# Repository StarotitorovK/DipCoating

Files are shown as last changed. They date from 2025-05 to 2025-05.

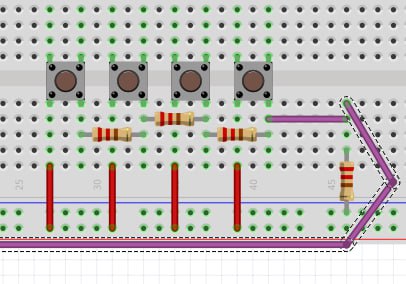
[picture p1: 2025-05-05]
Documentation/keyboard.jpg

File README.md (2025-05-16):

# DipCoater
------
Проект по практикуму цифрового производства

Прибор для нанесения тонких пленок методом dip-coating

Авторы:
	Старотиторов К.С., Б04-301
	Огай В.А., Б04-303

TG-канал: t.me/dip_coating

## Описание проекта

Поставленные задачи: 
выбрать доступный на рынке электромотор и систему преобразования вращательного движения в поступательное; определиться с основными материалами для производства, спроектировать основные узлы установки; изготовить детали и собрать установку; провести испытания в режиме proof of concept.

Описание установки:
продукт представляет собой устройство, состоящее из:

-	Корпуса, выполняющего также роль подставки для сосуда с мембранной массой;
-	Экрана с клавиатурой, с помощью которых настраиваются скорости погружения и вытягивания образца, а также время нахождения его в жидкости;
-	Рейки с мотором, к которой должен крепиться образец.






Используемый инструментарий:
3D-принтер, паяльная станция, профилометр 

Проблемы, с которыми мы встретились:
- Использование нескольких потребителей энергии добавляет сложностей в проектировке питания и запитки потребителей от одного источника.
- Для точности перемещения рейки требуется хорошая подгонка рейки в рельсе к шестерне.
- При переносе схемы клавиатуры с макетной платы вероятно изменились рассчитанные нами сопротивления, так что клавиатура сбоит и немного шумит, однако функционал может продемонстрировать.

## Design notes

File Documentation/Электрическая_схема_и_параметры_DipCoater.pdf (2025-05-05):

# Электрическая схема и параметры DipCoater

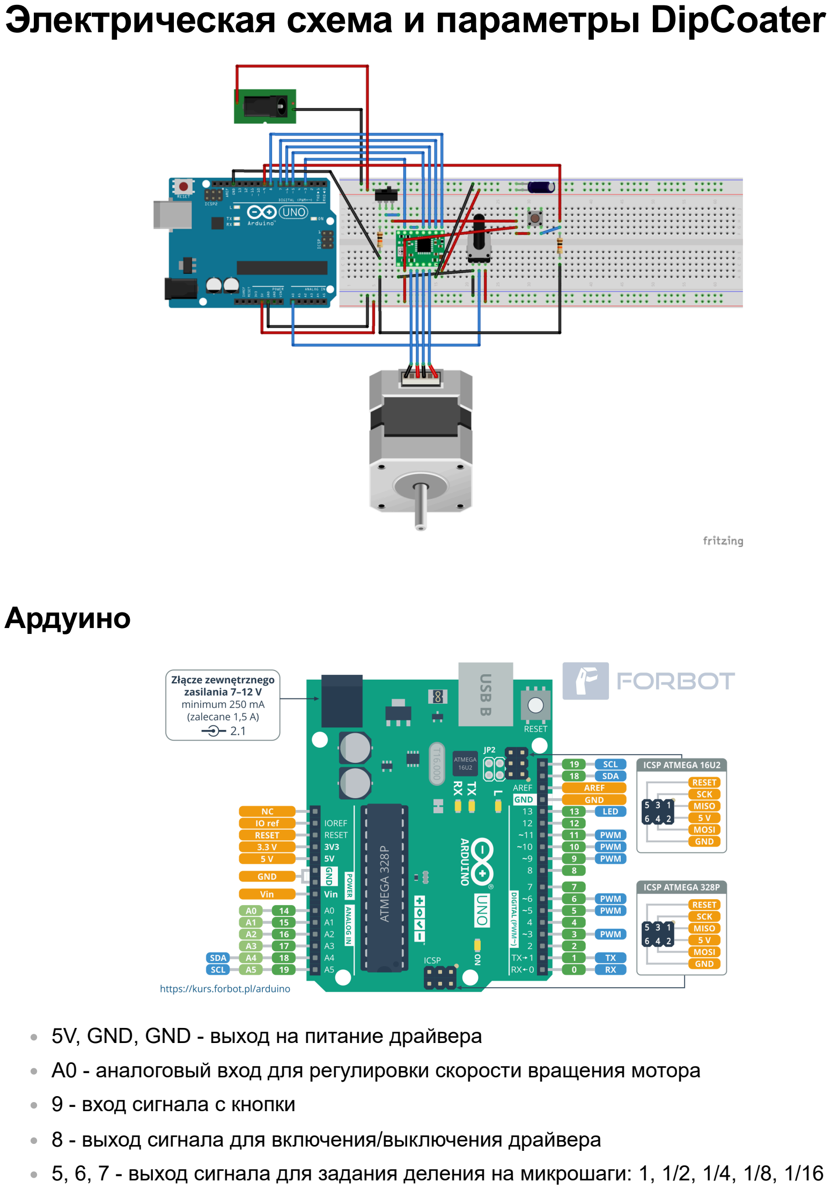
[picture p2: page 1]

## Ардуино

5V, GND, GND - выход на питание драйвера
A0 - аналоговый вход для регулировки скорости вращения мотора
9 - вход сигнала с кнопки
8 - выход сигнала для включения/выключения драйвера
5, 6, 7 - выход сигнала для задания деления на микрошаги: 1, 1/2, 1/4, 1/8, 1/16

## Драйвер

3 - выход сигнала для поворота вала двигателя

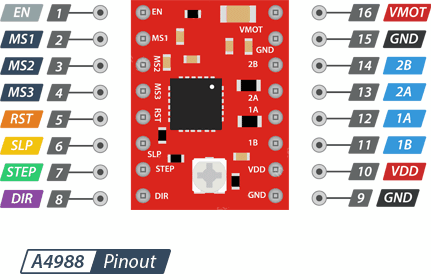
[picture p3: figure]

DIR вход подключен к переключателю: 1 - вращение по часовой стрелке, 0 - против RST и SLP - соединены, т.к. спящий режим не будет использоваться
VDD и GND - питание драйвера; подключены к 5V, GND платы Ардуино соответственно
VMT и GND - питание мотора; подключены через конденсатор 47мкФ к разъему PowerJack
MS1, MS2, MS3 - режим микрошага
1A, 1B, 2A, 2B - питание на обмотки электродвигателя
EN - включение/выключение драйвера: 0 - вкл, 1 - выкл STEP - совершение оборота электродвигателя: 1 - оборот.

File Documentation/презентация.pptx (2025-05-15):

## Проект по практикуму цифрового производства: Прибор для нанесения тонких пленок методом dip-coating.

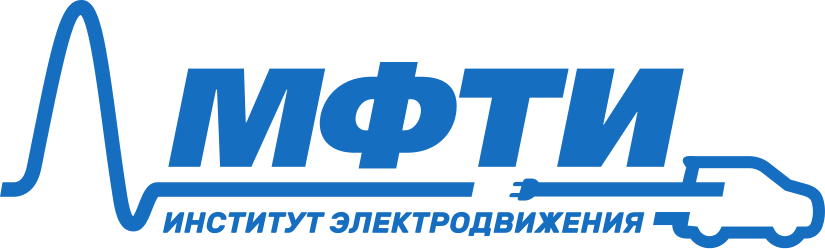
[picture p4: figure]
Изображение выглядит как Шрифт, текст, логотип, Графика Контент, сгенерированный ИИ, может содержать ошибки.

Старотиторов К.С., Огай В.А.
Московский физико-технический институт (НИУ)
2025 г.

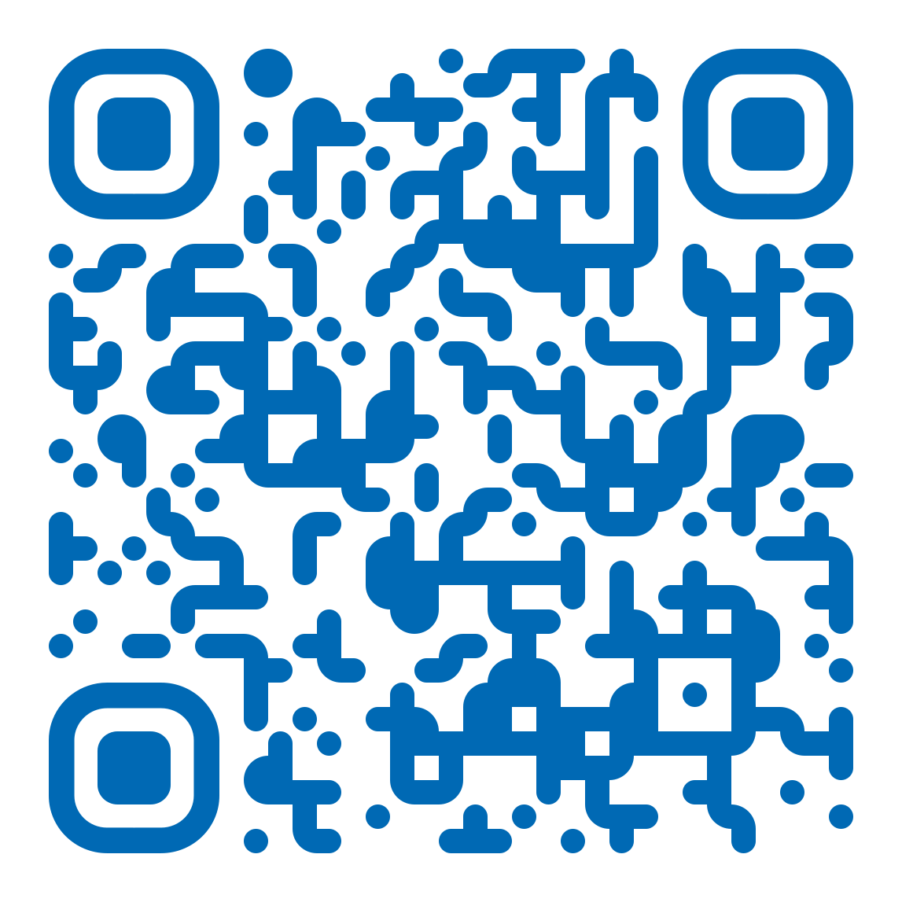
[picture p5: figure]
Изображение выглядит как Графика, Шрифт, типография, Цвет электрик Контент, сгенерированный ИИ, может содержать ошибки.

## Введение

- Литий-ионные аккумуляторы работают за счет перемещения ионов лития между электродами через электролит во время зарядки и разрядки.

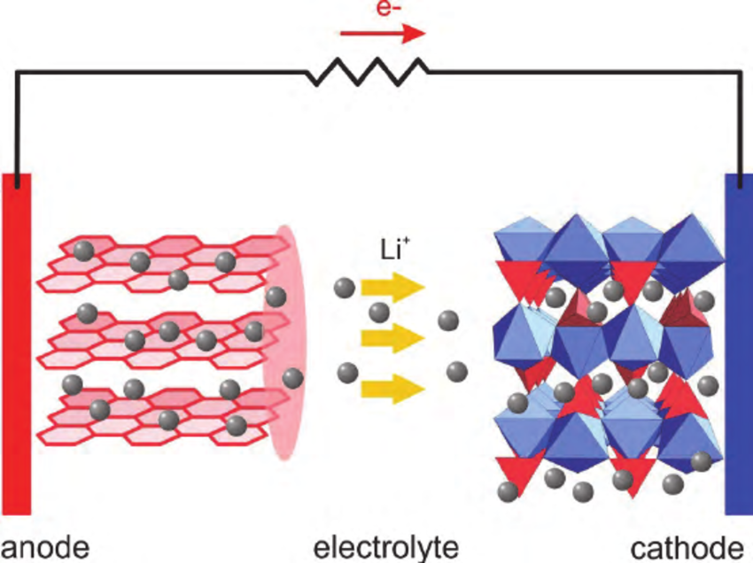
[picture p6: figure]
Working mechanism of Li-ion batteries. The effectiveness of the... | Download Scientific Diagram

## Введение

- Твердотельные литиевые аккумуляторы (ТЛА) – потенциально более безопасная, механически устойчивая и энергоемкая альтернатива классическим литий-ионным аккумуляторам с жидким электролитом (ЛИА)

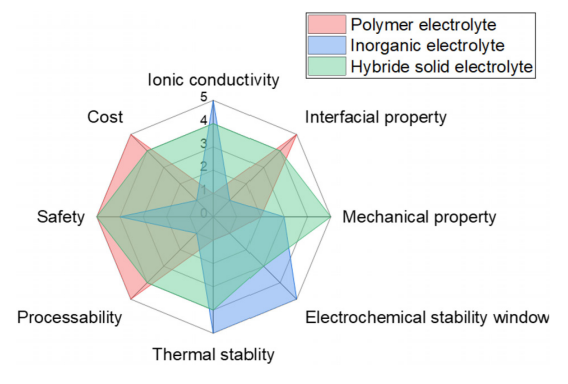
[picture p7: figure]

Неорганические электролиты

Полимерные электролиты

Ионная проводимость

Гибридные электролиты

Стоимость

Межфазное взаимодействие

Безопасность

Механические свойства

Технологичность

Термическая стабильность

Электрохимическая стабильность

## Способы создания мембран

Отдельно стоящая мембрана

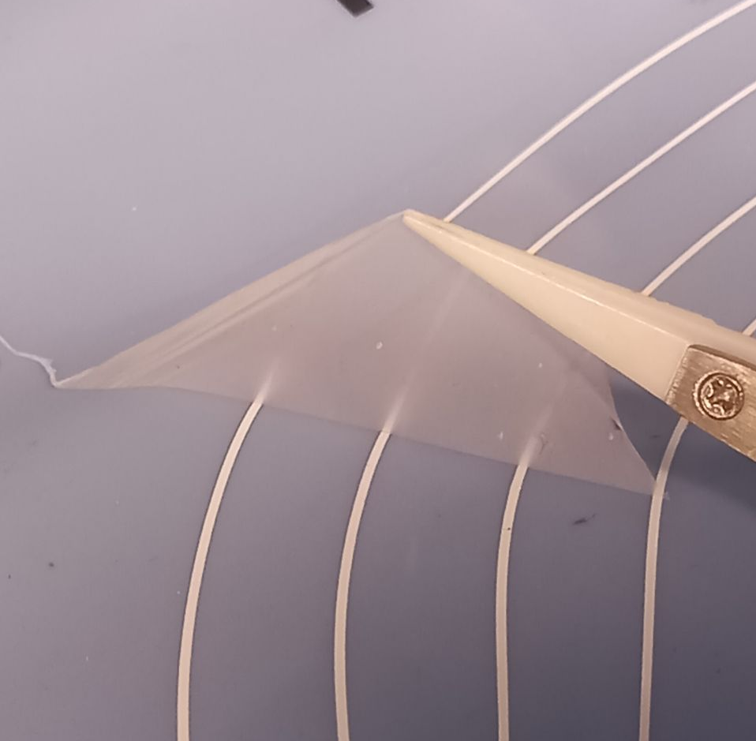
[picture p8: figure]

Spin-coating (на электрод)

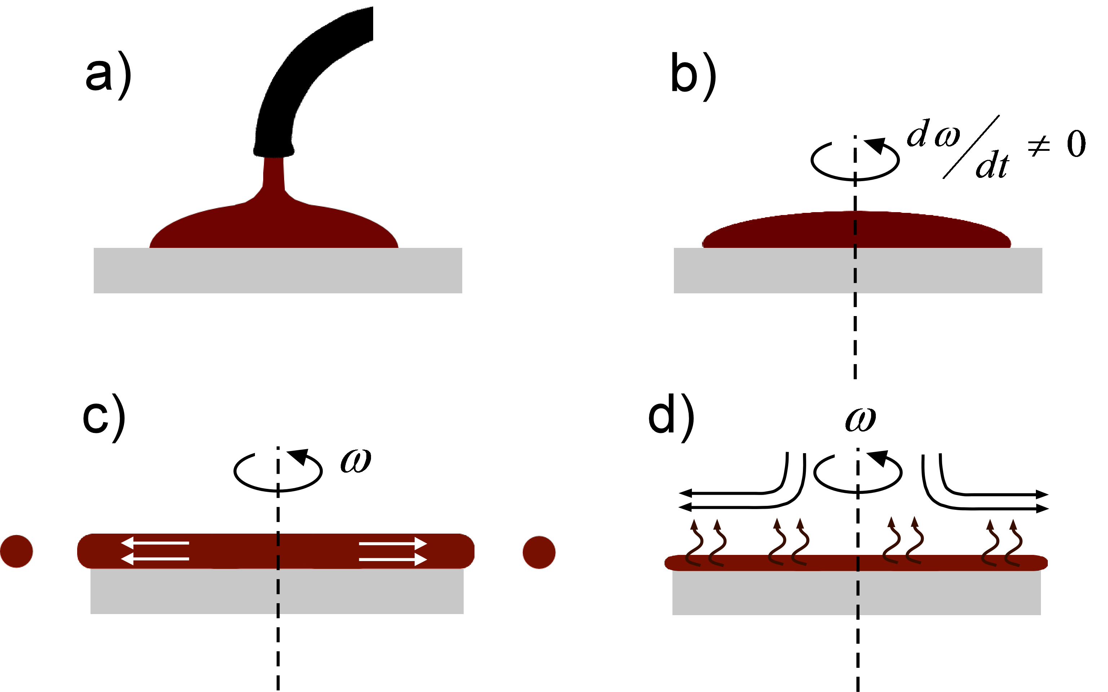
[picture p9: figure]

Blade-coating (на электрод)

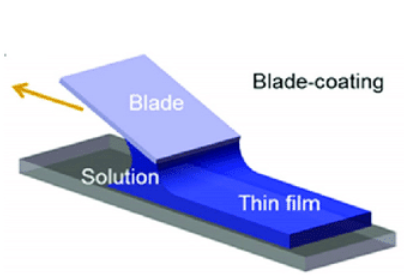
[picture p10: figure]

Dip-coating (на электрод)

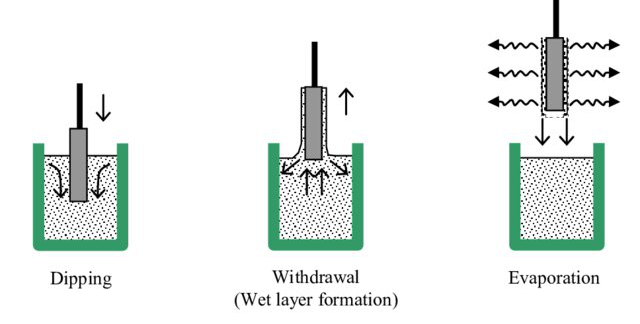
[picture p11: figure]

## Цель проекта и актуальность

- Цель проекта: спроектировать и изготовить прибор для нанесения тонких пленок (мембран) методом dip-coating с диапазоном скоростей покрытия 0,1-10 мм/с для лаборатории пост-литий-ионных электрохимических систем Института Электродвижения МФТИ.
- Актуальность: по предварительным подсчетам, себестоимость итогового продукта не будет превышать 15.000 руб., что в разы дешевле существующих на рынке решений.

## Теоретическая часть

- Зависимость толщины пленки от скорости извлечения, оставшейся на поверхности описывается капиллярной моделью (в области до 0,1 мм/с) и моделью Ландау-Левича (в области более 0,5 мм/с).
- Минимум толщины достигается в переходной области между двумя моделями.

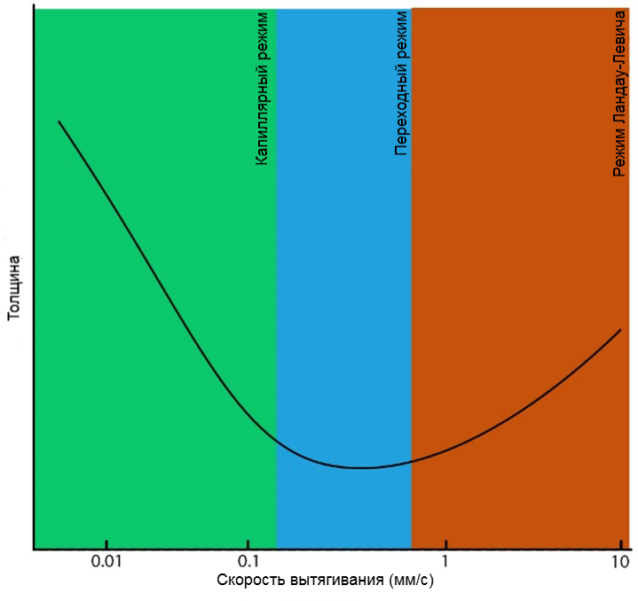
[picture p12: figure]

h=kE/(uL)

h=0,93((uη)^(2/3))/(σ^(1/6) √(ρg))

## Этапы проектирования

1. Разработка концепции работы устройства;
2. Создание прототипа без корпуса на базе Arduino Uno и макетной платы (код);
3. Тестирование прототипа на работоспособность;
4. 3D-моделирование и печать верхней части корпуса, рейки и шестерни;
5. Разработка клавиатуры;
6. 3D-моделирование и печать нижней части корпуса и крышки;
7. Пайка платы клавиатуры с кнопками;
8. Добавление клавиатуры и экрана к основной плате;
9. Итоговая сборка MVP;
10. Тестирование MVP (проверка работоспособности и удобства использования в лабораторных условиях).

## Принцип работы прибора с инженерной точки зрения

- Шаговый двигатель, установленный в корпус, используется для обеспечения движения с постоянной скоростью погружения и вытягивания образца.
- Вращательное движение мотора переводится в поступательное с помощью шестерни и зубчатой рейки, установленной в корпус на рельсу.

## 3D-модели компонентов прибора

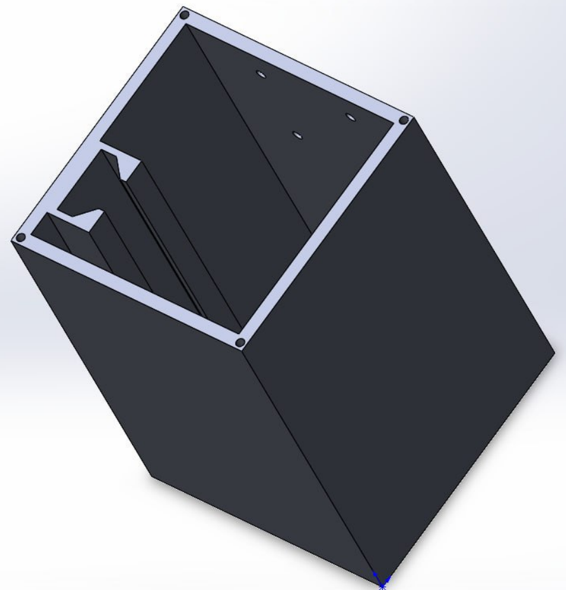
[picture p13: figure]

Корпус с желобом для рельсы и креплением для мотора

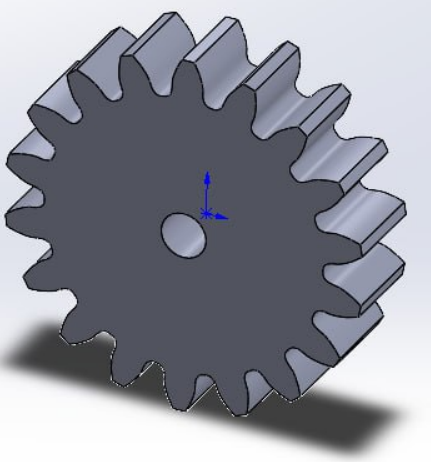
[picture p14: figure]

Шестерня

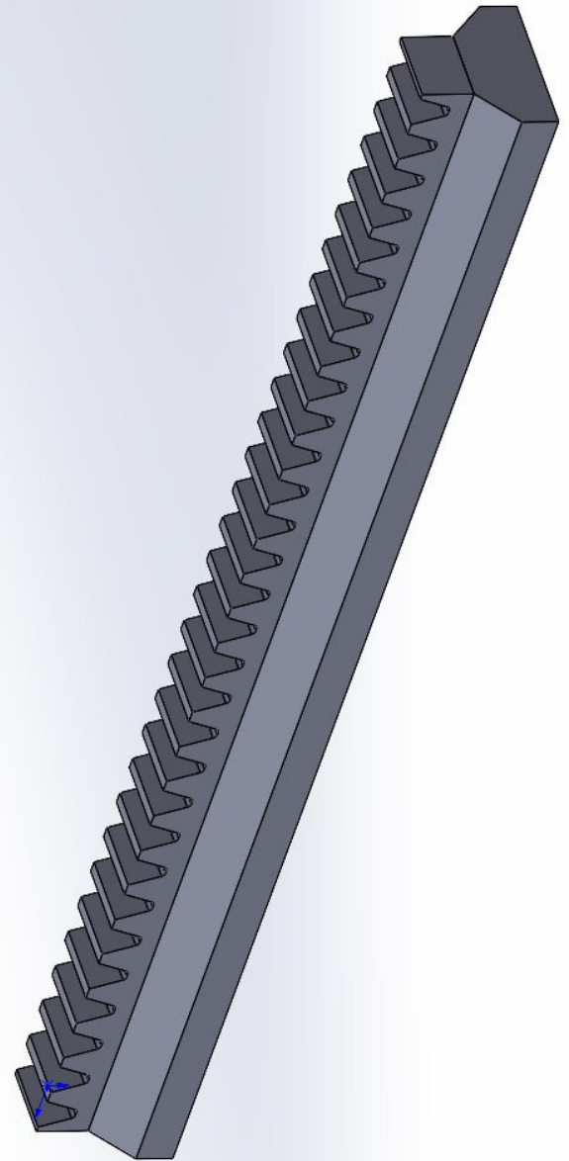
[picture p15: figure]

Зубчатая рейка на рельсе

## 3D-модели компонентов прибора

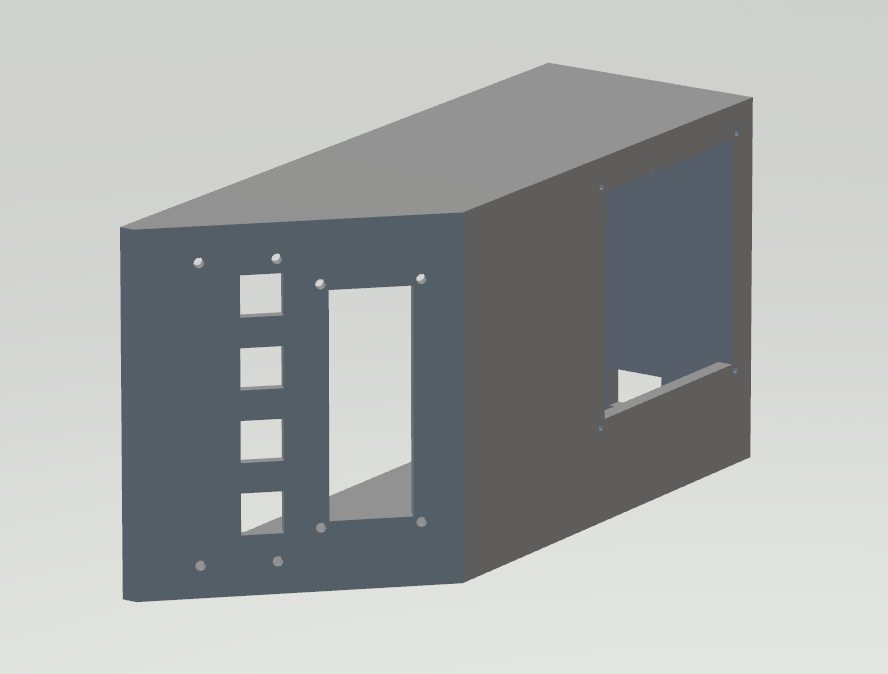
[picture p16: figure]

Нижняя часть корпуса

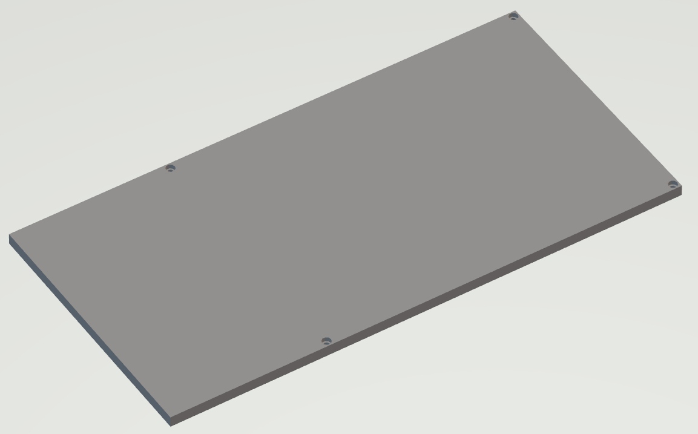
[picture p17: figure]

Крышка

## Аппаратная часть

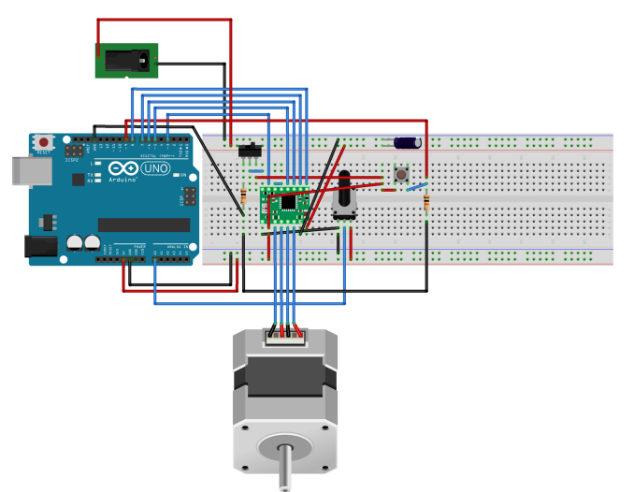
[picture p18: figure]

- Основными компонентами установки являются шаговый двигатель и плата Arduino Uno с драйвером, контролирующая его. Дополнительно возможно заменить используемую макетную плату на печатную, выполненную на заказ.

## Аппаратная часть (экран и клавиатура)

## Результаты тестирования

LiTFSI : PEO = 1 : 7,25

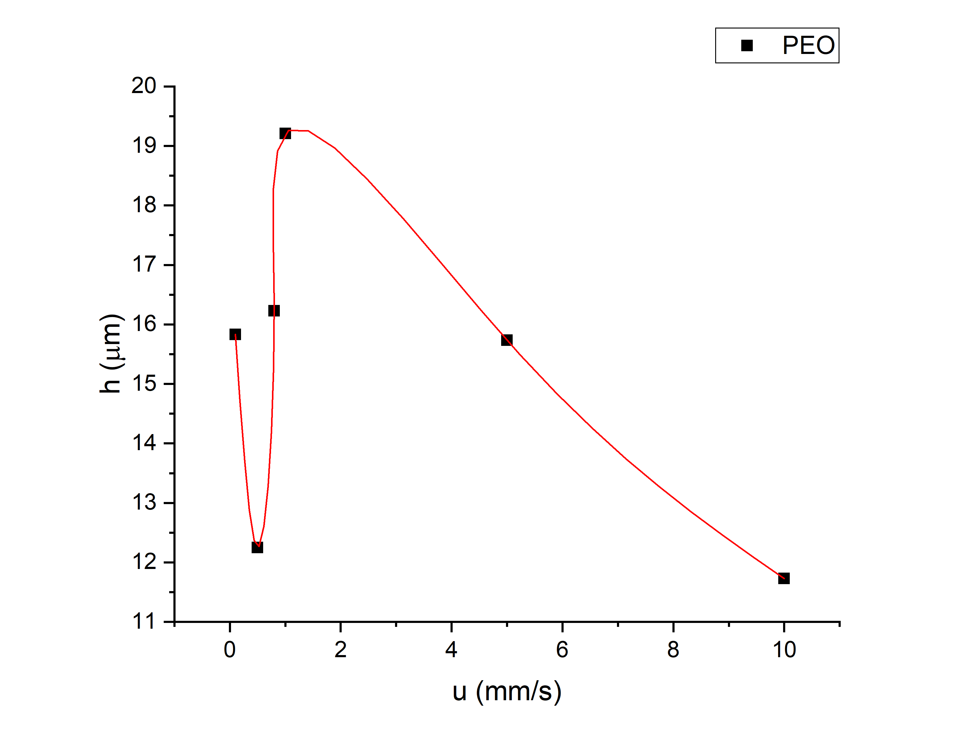
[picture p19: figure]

LiTFSI : SN : EO = 1 : 4 : 16

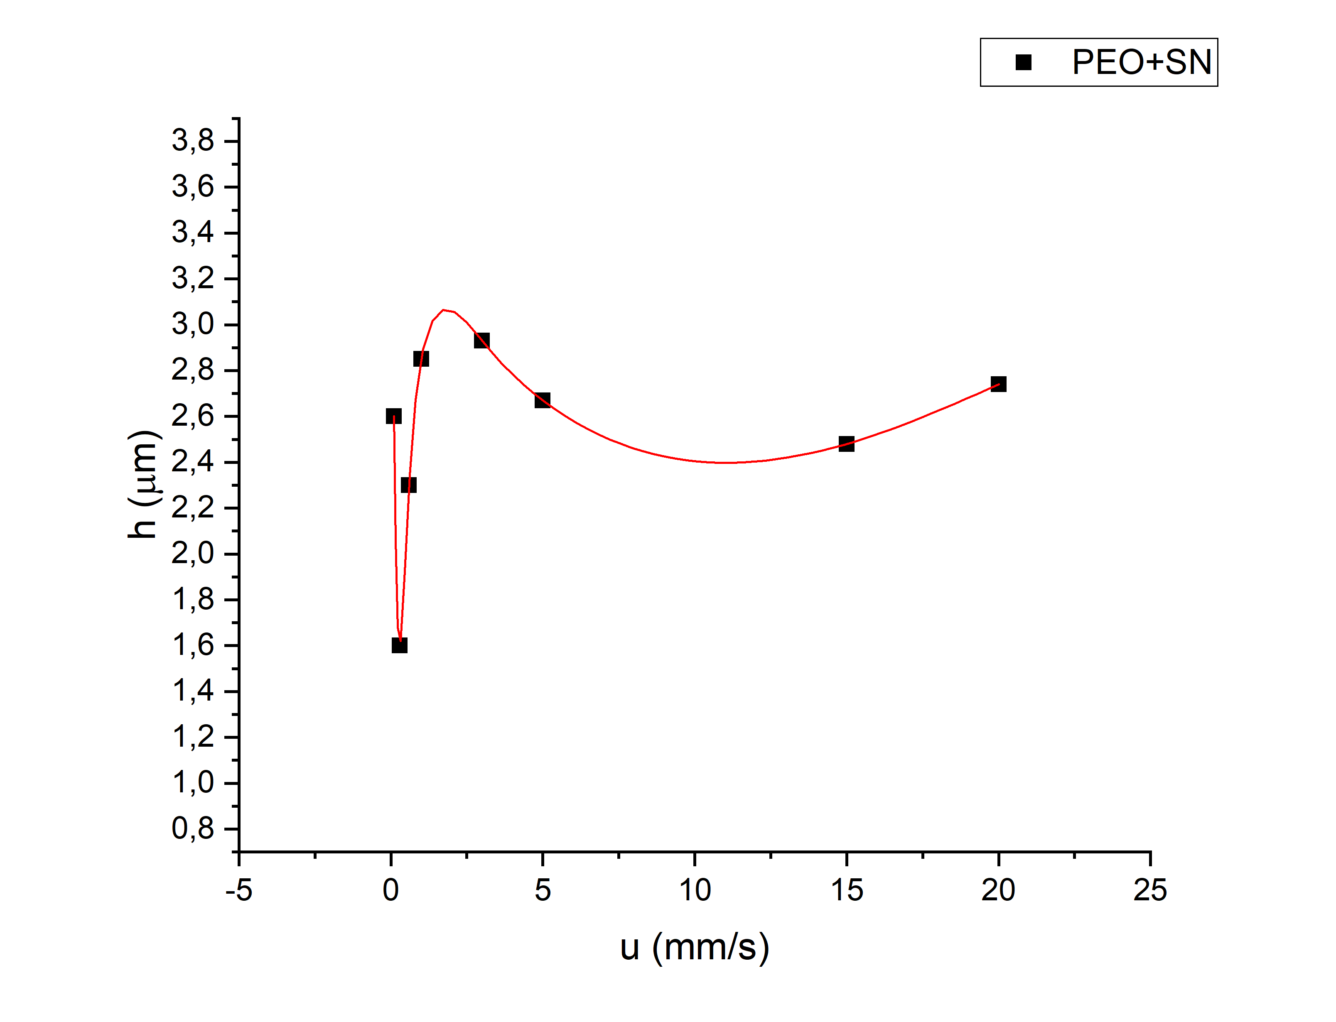
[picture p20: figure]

## Результаты тестирования

LiTFSI : PEO = 1 : 7,25

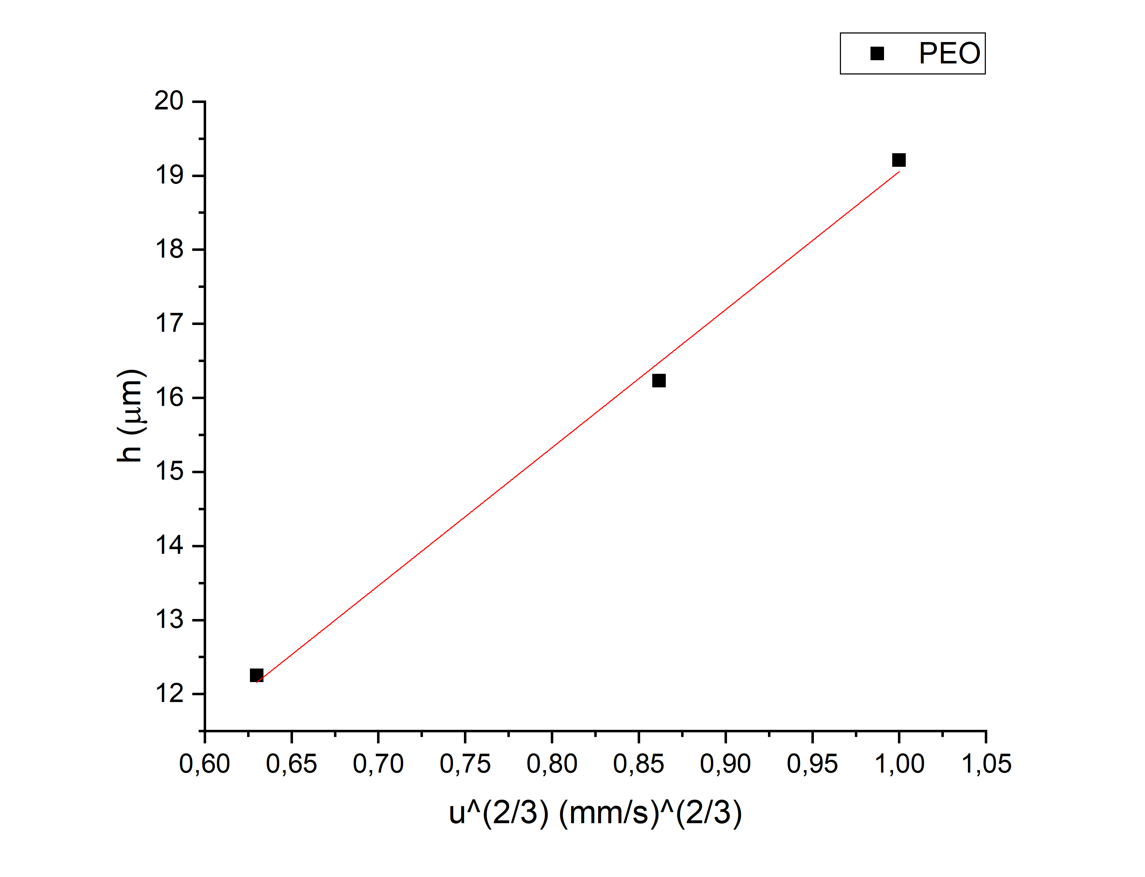
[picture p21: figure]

LiTFSI : SN : EO = 1 : 4 : 16

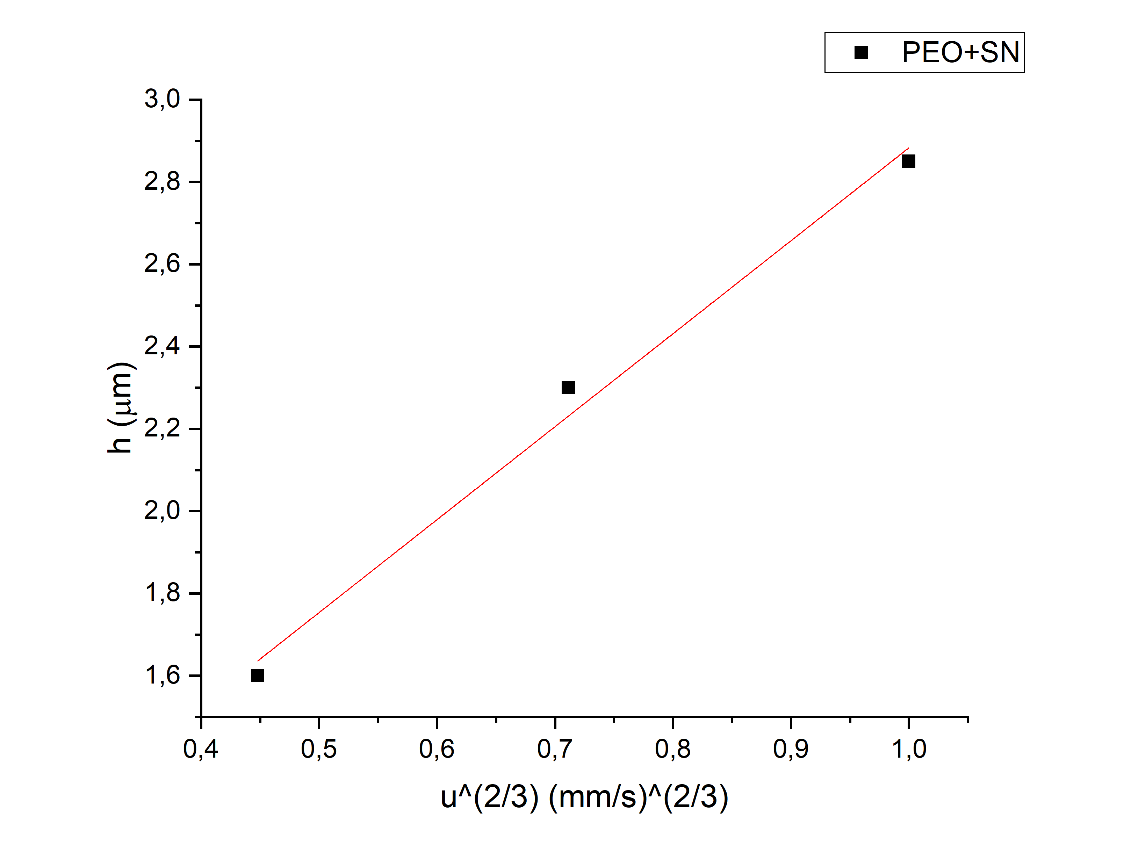
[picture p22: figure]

## Спасибо за внимание

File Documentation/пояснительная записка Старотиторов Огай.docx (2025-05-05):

Проект по практикуму цифрового производства:

Прибор для нанесения тонких пленок методом dip-coating.

Команда: Кирилл Старотиторов starotitorov.ks@phystech.edu, Владислав Огай ogai.va@phystech.edu

GitHub-репозиторий проекта (https://github.com/StarotitorovK/DipCoating)

Цель проекта: спроектировать и изготовить прибор для нанесения тонких пленок размером до 90*90 мм методом dip-coating с диапазоном скоростей покрытия 0.1-10 мм/с для лаборатории пост-литий-ионных электрохимических решений Института Электродвижения МФТИ.

Задачи проекта: выбрать доступный на рынке электромотор и систему преобразования вращательного движения в поступательное; определиться с основными материалами для производства, спроектировать основные узлы установки; изготовить детали и собрать установку; провести испытания в режиме proof of concept.

Причина выбора проекта: необходимость изучения и разработки твердотельных литий-ионных аккумуляторов в Институте Электродвижения, и, следовательно, создание образцов с постоянными, неизменными от случая к случаю характеристиками, а именно ионопроводящих мембран, которые и будут наноситься с помощью данного устройства.

Существующие аналоги:

1. Jikan DCM-10 (https://www.jikangroup.com/products/coating-machines/dcm-10/) - это лабораторное устройство для нанесения покрытий методом погружения. Устройство имеет широкий диапазон скоростей и времени остановки и может быть запрограммировано на нужные циклы.
2. Dip Coater by Ossila (https://www.ossila.com/products/dip-coater) имеет схожий функционал с Jikan DCM-10, но более компактные размеры.

Эскиз проекта:

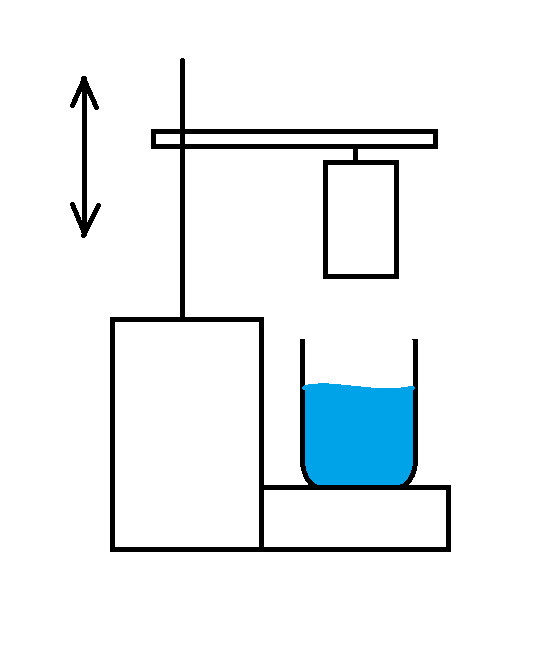
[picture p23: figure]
Изображение выглядит как диаграмма, Прямоугольник, линия, дизайн Контент, сгенерированный ИИ, может содержать ошибки.

Описание продукта: продукт представляет собой устройство, состоящее из:

- Корпуса, выполняющего также роль подставки для сосуда с мембранной массой (3D-модели в репозитории: верхняя (https://github.com/StarotitorovK/DipCoating/blob/master/3D%20models/body.STL), нижняя (https://github.com/StarotitorovK/DipCoating/blob/master/3D%20models/corpus_bottom.stl) части корпуса, нижняя крышка (https://github.com/StarotitorovK/DipCoating/blob/master/3D%20models/corpus_cover.stl));
- Экрана с клавиатурой, с помощью которых настраиваются скорости погружения и вытягивания образца, а также время нахождения его в жидкости (электрическая схема клавиатуры (https://github.com/StarotitorovK/DipCoating/blob/master/Documentation/keyboard.jpg));
- Рейки с мотором, к которой должен крепиться образец (3D-модель рейки (https://github.com/StarotitorovK/DipCoating/blob/master/3D%20models/RackWithBase.STL) и шестерни (https://github.com/StarotitorovK/DipCoating/blob/master/3D%20models/Gear.STL), электрическая схема (https://github.com/StarotitorovK/DipCoating/blob/master/Documentation/Электрическая_схема_и_параметры_DipCoater.pdf)).

Проектирование и изготовление: проходили следующими этапами:

1. Разработка концепции работы устройства;
2. Создание прототипа без корпуса на базе Arduino Uno и макетной платы (код (https://github.com/StarotitorovK/DipCoating/tree/master/code));
3. Тестирование прототипа на работоспособность;
4. 3D-моделирование и печать верхней части корпуса, рейки и шестерни;
5. Разработка клавиатуры;
6. 3D-моделирование и печать нижней части корпуса и крышки;
7. Пайка платы клавиатуры с кнопками;
8. Добавление клавиатуры и экрана к основной плате;
9. Итоговая сборка MVP;
10. Тестирование MVP (проверка работоспособности и удобства использования в лабораторных условиях).

Роли и личный вклад участников команды:

Старотиторов Кирилл – программист-разнорабочий. Разрабатывал логику и код проекта, проводил полевое тестирование прототипа, моделировал верхнюю часть корпуса, шестерню и рейку.

Огай Владислав – пайщик, разнорабочий. Моделировал нижнюю часть корпуса и нижнюю крышку, паял клавиатуру и проводил физическую обработку и доработку корпуса.

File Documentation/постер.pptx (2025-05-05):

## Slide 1

Проект по практикуму цифрового производства:
Прибор для нанесения тонких пленок методом dip-coating.
Огай В.А.¹, Старотиторов К.С.¹, 2025 год

Модель Ландау-Левича

Модель Ландау–Левича описывает процесс формирования тонкой жидкой пленки на поверхности, медленно извлекаемой из жидкости. Согласно этой модели, толщина пленки h зависит от скорости вытягивания u, вязкости жидкости η, поверхностного натяжения γ и плотности жидкости ρ. В упрощённом виде, при низких скоростях и в условиях ламинарного течения, толщина пленки выражается как:
h=0,93((uη)^(2/3))/(σ^(1/6) √(ρg))
(при рассмотрении образца как бесконечной поверхности, т.е. без учета толщины на краях)

Разработка продукта (MVP)

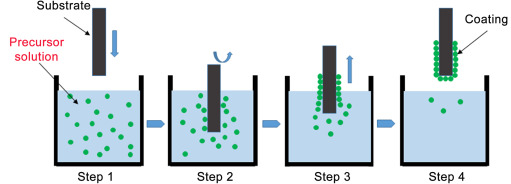
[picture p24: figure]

Цель проекта и актуальность:
- Цель проекта: спроектировать и изготовить прибор для нанесения тонких пленок (мембран) методом dip-coating с диапазоном скоростей покрытия 1-10 мм/с для лаборатории пост-литий-ионных электрохимических систем Института Электродвижения МФТИ.
- Актуальность: по предварительным подсчетам, себестоимость итогового продукта не будет превышать 15.000 руб., что в разы дешевле существующих на рынке решений.
Ход разработки:
- Прототипирование на базе Arduino Uno (написание кода и разработка логики устройства);
- 3D-моделирование и печать частей корпуса, рейки и шестерни;
- Пайка клавиатуры и сборка MVP;
- Финальное тестирование и отладка.

¹ Московский физико-технический институт (национальный исследовательский университет), г. Долгопрудный

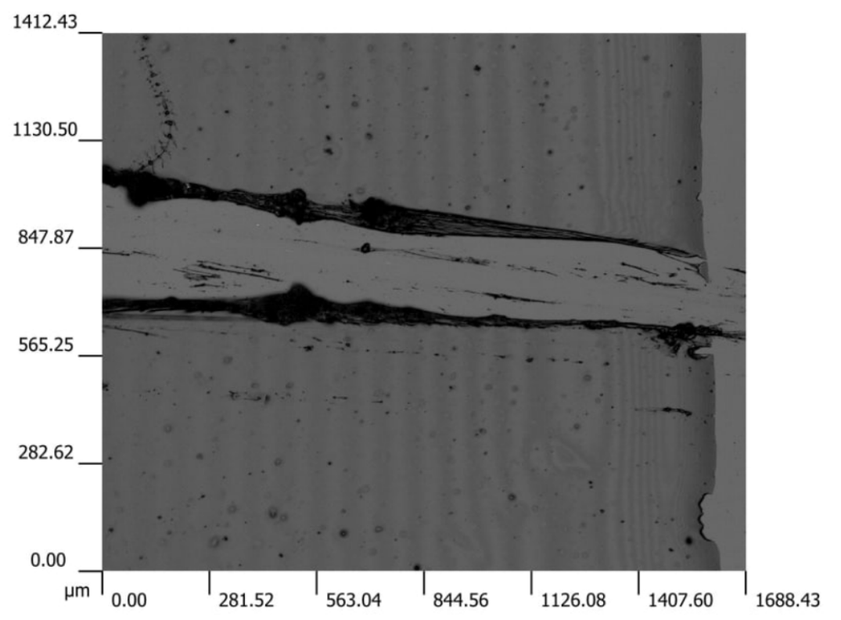
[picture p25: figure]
Изображение выглядит как Графика, Шрифт, типография, Цвет электрик Контент, сгенерированный ИИ, может содержать ошибки.
Изображение выглядит как Шрифт, текст, логотип, Графика Контент, сгенерированный ИИ, может содержать ошибки.

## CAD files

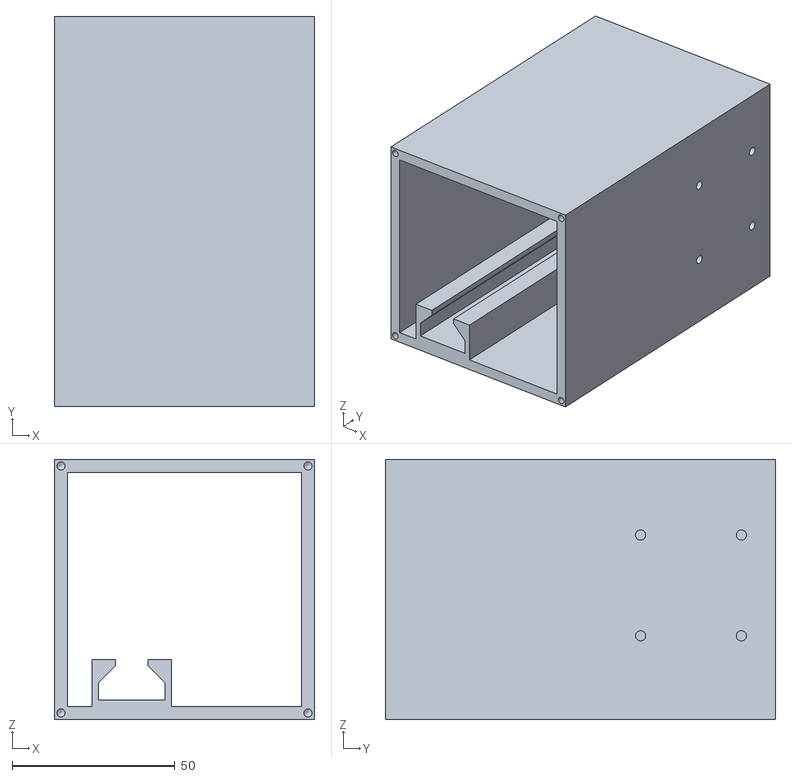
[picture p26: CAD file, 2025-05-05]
3D models/body.STL
80.0 x 120.0 x 80.0

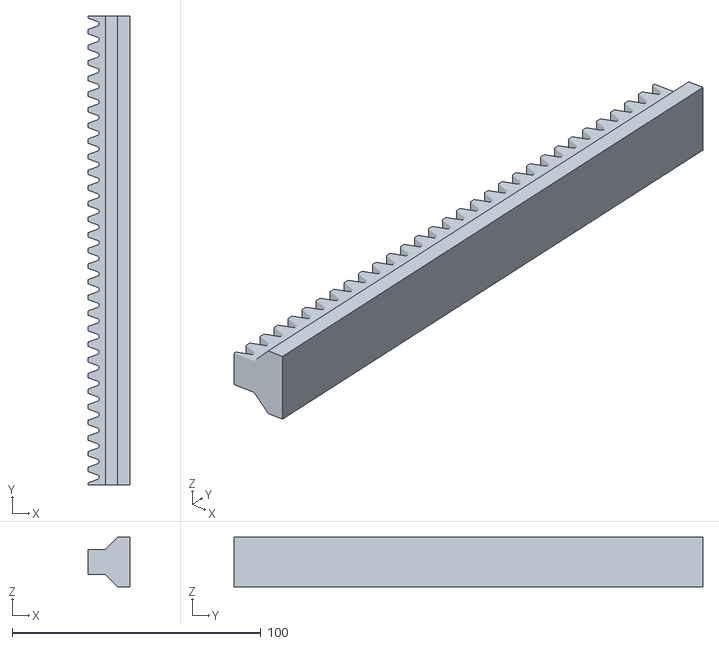
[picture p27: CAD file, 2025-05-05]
3D models/RackWithBase.STL
17.0 x 188.5 x 20.0

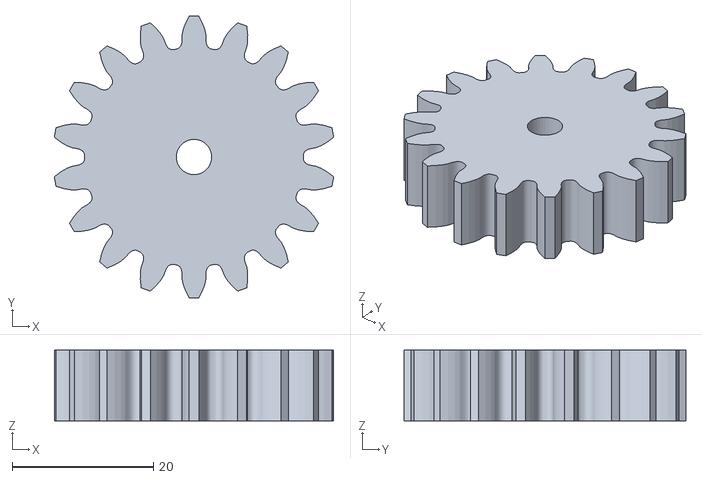
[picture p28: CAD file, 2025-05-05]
3D models/Gear.STL
39.6 x 40.0 x 10.0

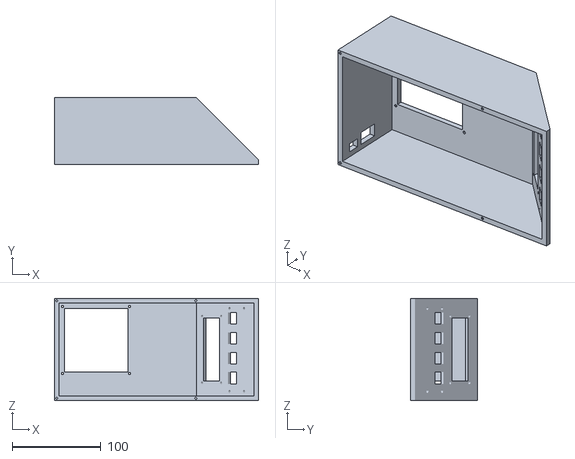
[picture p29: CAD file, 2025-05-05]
3D models/corpus_bottom.stl
230.0 x 75.0 x 115.0

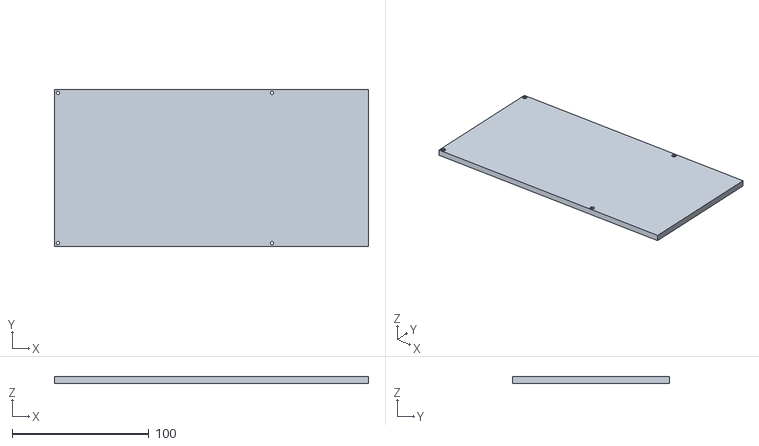
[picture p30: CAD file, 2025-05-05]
3D models/corpus_cover.stl
230.0 x 115.0 x 5.00

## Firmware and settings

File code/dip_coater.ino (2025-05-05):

#include "AnalogButtons.h"
#include "Control.h"
#include "Display.h"
#include "GyverStepper2.h"

#define DEBUG_ENABLE

#ifdef DEBUG_ENABLE
#define DEBUG(x) Serial.println(x)
#else
#define DEBUG(x)
#endif

int KEYBOARD = A0;
int STEP = 5;                  // Светодиод подсоединен к цифровому выводу 13
int DIR = 4;
int EN = 6;
int D4 = 10;
int D5 = 11;
int D6 = 12;
int D7 = 13;
int RS = 7;
int RW = 8;
int E = 9;

LcdDisplay display(RS, RW, E, D4, D5, D6, D7);
GStepper2< STEPPER2WIRE> stepper(400, STEP, DIR);
bool manualCoatingFlag = false;
bool dir = true;

void setup() {
  #ifdef DEBUG_ENABLE
  Serial.begin(9600);
  #endif


  display.init();
  initAnalogButtons(KEYBOARD); 
  initMenu(display);


  pinMode(STEP, OUTPUT);       // устанавливаем режим работы вывода, как "выход"
  pinMode(DIR, OUTPUT);
  pinMode(EN, OUTPUT);

  digitalWrite(DIR, LOW);
  digitalWrite(EN, LOW);
}

void loop() {
  Button btn = readAnalogButton(KEYBOARD);
  manualCoatingFlag = false;

  switch (btn) {
    case UP:
        if (currentScreen == MAIN_SCREEN) manual_coating(true);
        else if (currentScreen == MENU_SCREEN) {
            currentOptionIndex--;
            if (currentOptionIndex < 0) currentOptionIndex = getMaxMenuIndex();
        }
        else if (currentScreen == OPTION_SCREEN && options[currentOptionIndex].onUp) {
            options[currentOptionIndex].onUp();
            showOptionDisplay(display);
        }
      break;
    case DOWN:
        if (currentScreen == MAIN_SCREEN) manual_coating(false);
        else if (currentScreen == MENU_SCREEN) {
            currentOptionIndex++;
            if (currentOptionIndex > getMaxMenuIndex()) currentOptionIndex = 0;
        }
        else if (currentScreen == OPTION_SCREEN && options[currentOptionIndex].onDown) {
            options[currentOptionIndex].onDown();
            showOptionDisplay(display);
        }
      break;
    case MENU:
        if (currentScreen == MAIN_SCREEN) {
            currentScreen = MENU_SCREEN;
        } else if (currentScreen == MENU_SCREEN) {
            currentScreen = MAIN_SCREEN;
        } else if (currentScreen == OPTION_SCREEN && options[currentOptionIndex].onCancel) {
            options[currentOptionIndex].onCancel();
            currentScreen = MENU_SCREEN;
        }
      break;
    case START:
        if (currentScreen == MAIN_SCREEN) startProcess();
        else if (currentScreen == MENU_SCREEN) currentScreen = OPTION_SCREEN;
        else if (currentScreen == OPTION_SCREEN && options[currentOptionIndex].onEnter)
            options[currentOptionIndex].onEnter();
      break;
    default:
      break;
  }
  
  updateMenu(display);
  delay(200);
}


// void loop()
// {
//   digitalWrite(STEP, HIGH);   
//   delay(20);                   
//   digitalWrite(STEP, LOW);    
//   delay(20);                   
// }

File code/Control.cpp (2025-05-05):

#include "Control.h"
#include "Display.h"
#include <EEPROM.h>

CoatingParameters parameters = { 1.0, 1.0, 0.0 };
Screen currentScreen = MAIN_SCREEN;
int currentOptionIndex = 0;

Option options[3] = {
    { "Speed", speedUp, speedDown, saveOptions, loadParameters },
    { "Height", toggleSizeUp, toggleSizeDown, saveOptions, loadParameters },
    { "Wait", waitUp, waitDown, saveOptions, loadParameters }
};

void initMenu(LcdDisplay& display) {
    currentScreen = MAIN_SCREEN;
    currentOptionIndex = 0;
    showMainDisplay(display);
}

void updateMenu(LcdDisplay& display) {
    switch (currentScreen) {
    case MAIN_SCREEN:
        showMainDisplay(display);
        break;
    case MENU_SCREEN:
        showMenuDisplay(display);
        break;
    case OPTION_SCREEN:
        showOptionDisplay(display);
        break;
    }
}

void showMainDisplay(LcdDisplay& display) {
    display.clear();
    display.printLine(0, "Press start");
    display.printLine(1, "to coat");
}

void showMenuDisplay(LcdDisplay& display) {
    display.clear();
    display.printLine(0, options[currentOptionIndex].name);
}

void showOptionDisplay(LcdDisplay& display) {
    display.clear();
    display.printLine(0, options[currentOptionIndex].name);
    updateOptionDisplay(display);
}

void updateOptionDisplay(LcdDisplay& display) {
    auto val = String(parameters[currentOptionIndex]);
    display.printLine(1, val);
}

void speedUp() {
    if ((parameters.speed >= 1.0) && (parameters.speed <= 19.5)) {
        if (parameters.speed <= 10.0) parameters.speed += 0.1;
        else if (parameters.speed <= 20.0) parameters.speed += 0.5;
    }
}
void speedDown() {
    if ((parameters.speed >= 1.1) && (parameters.speed <= 20.0)) {
        if (parameters.speed <= 10.0) parameters.speed -= 0.1;
        else if (parameters.speed <= 20.0) parameters.speed -= 0.5;
    }
}

void toggleSizeUp() {
    if ((parameters.coating_distance >= 1.0) && (parameters.coating_distance <= 7.9)) {
        parameters.coating_distance += 0.1;
    }
}
void toggleSizeDown() {
    if ((parameters.coating_distance >= 1.1) && (parameters.coating_distance <= 8.0)) {
        parameters.coating_distance -= 0.1;
    }
}

void waitUp() {
    if ((parameters.wait >= 0.0) && (parameters.wait <= 9.9)) {
        parameters.wait += 0.1;
    }
}

void waitDown() {
    if ((parameters.wait >= 0.1) && (parameters.wait <= 10.0)) {
        parameters.wait -= 0.1;
    }
}


void saveOptions() {
  EEPROM.put(0, parameters);
}

void loadParameters() {
  EEPROM.get(0, parameters);

  if (isnan(parameters.speed) || isnan(parameters.coating_distance) || isnan(parameters.wait)) {
    parameters = {1.0f, 1.0f, 0.0f};
    saveOptions();
  }
}


float evaluateSPS(float speed, int steps) {
    float i = 1; // передаточное число редуктора
	float d = 40; // диаметр шестерни
	return steps * i * speed / (d * 3.14); // скорость в шаг/с
}

float evaluateAccel(float speed, int steps) {
	return evaluateSPS(speed, steps) * speed; // ускорение в шаг/с^2
}

void startProcess() {
    stepper.setMaxSpeed(evaluateSPS(parameters.speed, 6400));    
    stepper.setAcceleration(evaluateAccel(parameters.speed, 6400));
    stepper.setTarget(6400 * 3);

    while (!stepper.ready()) {
        stepper.tick(); 
    }
}

void manual_coating(bool dir) {
    // реализуй ручное управление
}

int getMaxMenuIndex() {
    return 2; 
}
